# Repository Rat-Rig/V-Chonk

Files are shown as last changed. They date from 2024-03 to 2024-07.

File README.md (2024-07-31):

<a href="https://ratrig.com/">
    RatRig logo RatRig
</a>

# Rat Rig V-Chonk v0.4 BETA
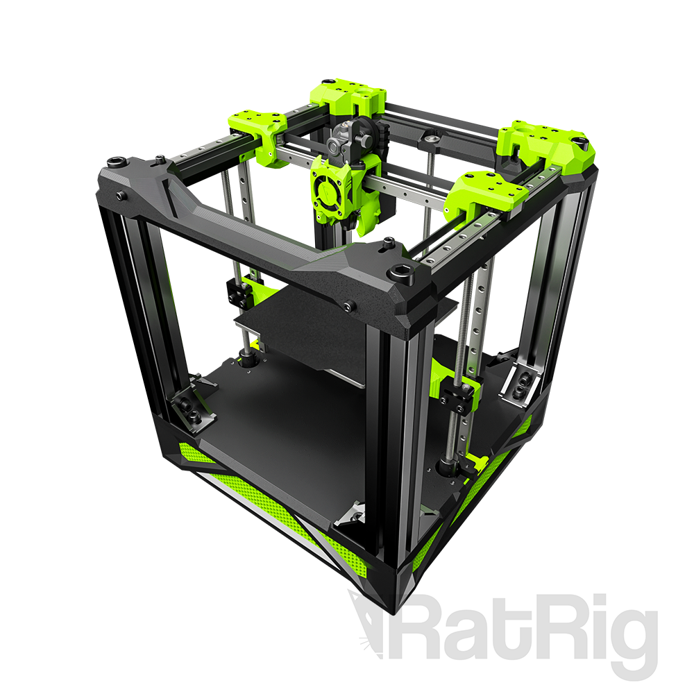
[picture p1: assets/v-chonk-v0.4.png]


## Overview
The Rat Rig V-Chonk is an almost fully 3D printed 3D printer, featuring a CoreXY design and a cubic build volume of 180mm<sup>3</sup>

Full details can be found on [the Rat Rig store](https://ratrig.com/v-chonk-configurable.html), or [the USA Rat Rig store](https://us.ratrig.com/v-chonk-configurable.html)

## Online CAD Viewer
Two different CAD models are available for viewing online:
- [V-Chonk with HF hotend](https://a360.co/3A7DrUY)
- [V-Chonk with UHF hotend](https://a360.co/3A2c6U1)

## STEP Files
Both variants of the CAD model are also available for download in the STEP format:
- [V-Chonk with HF hotend STEP Download](https://files.ratrig.com/cad_models/vchonk/ratrig_v-chonk_v0.4_hf.zip)
- [V-Chonk with UHF hotend STEP Download](https://files.ratrig.com/cad_models/vchonk/ratrig_v-chonk_v0.4_uhf.zip)

## Contributing
This is a fully open source project! We encourage the community at large to mod, upgrade, and share their design variants.

Join our communities and connect with other users, we would love to see some great V-Chonk builds:

Facebook - https://www.facebook.com/groups/ratrig3dprintercommunity

Discord - https://discord.com/invite/ratrig

## License
All files contained within this repository are licensed under the [Creative Commons Attribution-ShareAlike 4.0 International Public License](https://creativecommons.org/licenses/by-sa/4.0/). See LICENSE for the full details.

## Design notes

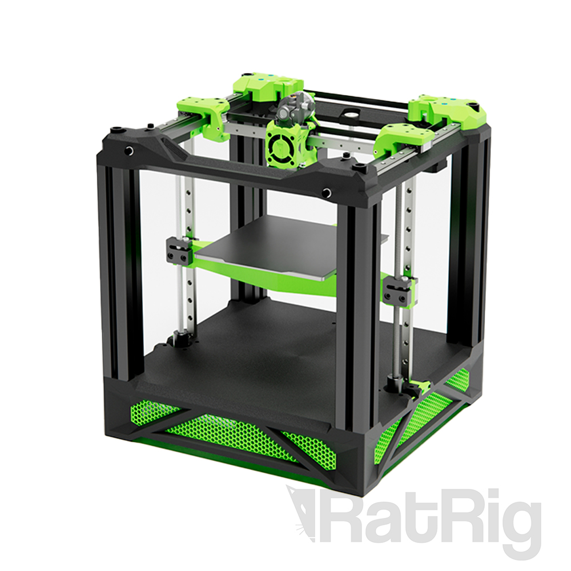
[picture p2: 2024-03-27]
assets/v-chonk-v0.2.jpg

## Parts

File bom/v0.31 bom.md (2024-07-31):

# Bill of Materials

## Printed Parts
| Quantity | Part Name | Link |
| --- | --- | ---- |
| 1x | chonk_base_plate | [chonk_base_plate_V03_20240509.stl](https://github.com/Rat-Rig/V-Chonk/blob/main/stl/Deprecated/chonk_base_plate_V03_20240509.stl) |
| 1x | chonk_bed_carriage | [chonk_bed_carriage_V02_20240606.stl](https://github.com/Rat-Rig/V-Chonk/blob/main/stl/chonk_bed_carriage_V02_20240606.stl) |
| 1x | chonk_belt_pod_a | [chonk_belt_pod_a_V02_20240411.stl](https://github.com/Rat-Rig/V-Chonk/blob/main/stl/chonk_belt_pod_a_V02_20240411.stl) |
| 1x | chonk_belt_pod_b | [chonk_belt_pod_b_V02_20240411.stl](https://github.com/Rat-Rig/V-Chonk/blob/main/stl/Deprecated/chonk_belt_pod_b_V02_20240411.stl) |
| 1x | chonk_belt_pod_c | [chonk_belt_pod_c_V01_20240411.stl](https://github.com/Rat-Rig/V-Chonk/blob/main/stl/Deprecated/chonk_belt_pod_c_V01_20240411.stl) |
| 2x | chonk_belt_tensioner | [chonk_belt_tensioner_x2_V01_20240329.stl](https://github.com/Rat-Rig/V-Chonk/blob/main/stl/chonk_belt_tensioner_x2_V01_20240329.stl) |
| 1x | chonk_motor_cage_a | [chonk_motor_cage_a_V01_20240329.stl](https://github.com/Rat-Rig/V-Chonk/blob/main/stl/chonk_motor_cage_a_V01_20240329.stl) |
| 1x | chonk_motor_cage_b | [chonk_motor_cage_b_V01_20240329.stl](https://github.com/Rat-Rig/V-Chonk/blob/main/stl/chonk_motor_cage_b_V01_20240329.stl) |
| 1x | chonk_skirt_back | [chonk_skirt_back_V01_20240329.stl](https://github.com/Rat-Rig/V-Chonk/blob/main/stl/chonk_skirt_back_V01_20240329.stl) |
| 4x | chonk_skirt_foot | [chonk_skirt_foot_V02_20240509.stl](https://github.com/Rat-Rig/V-Chonk/blob/main/stl/chonk_skirt_foot_V02_20240509.stl) |
| 1x | chonk_skirt_front | [chonk_skirt_front_V01_20240329.stl](https://github.com/Rat-Rig/V-Chonk/blob/main/stl/chonk_skirt_front_V01_20240329.stl) |
| 2x | chonk_skirt_side | [chonk_skirt_side_x2_V01_20240329.stl](https://github.com/Rat-Rig/V-Chonk/blob/main/stl/chonk_skirt_side_x2_V01_20240329.stl) |
| 1x | chonk_toolhead_hf | [chonk_toolhead_hf_V01_20240411.stl](https://github.com/Rat-Rig/V-Chonk/blob/main/stl/Deprecated/chonk_toolhead_hf_V01_20240411.stl) |
| 1x | chonk_toolhead_uhf | [chonk_toolhead_uhf_V01_20240411.stl](https://github.com/Rat-Rig/V-Chonk/blob/main/stl/Deprecated/chonk_toolhead_uhf_V01_20240411.stl) |
| 1x | chonk_xy_gantry | [chonk_xy_gantry_V01_20240329.stl](https://github.com/Rat-Rig/V-Chonk/blob/main/stl/Deprecated/chonk_xy_gantry_V01_20240329.stl) |
| 1x | chonk_xy_joiner_a | [chonk_xy_joiner_a_V01_20240329.stl](https://github.com/Rat-Rig/V-Chonk/blob/main/stl/chonk_xy_joiner_a_V01_20240329.stl) |
| 1x | chonk_xy_joiner_b | [chonk_xy_joiner_b_V01_20240329.stl](https://github.com/Rat-Rig/V-Chonk/blob/main/stl/chonk_xy_joiner_b_V01_20240329.stl) |
| 2x | chonk_z_rail_clamp_bottom | [chonk_z_rail_clamp_bottom_V01_20240329.stl](https://github.com/Rat-Rig/V-Chonk/blob/main/stl/chonk_z_rail_clamp_bottom_V01_20240329.stl) |
| 2x | chonk_z_rail_clamp_top | [chonk_z_rail_clamp_top_x2_V01_20240329.stl](https://github.com/Rat-Rig/V-Chonk/blob/main/stl/chonk_z_rail_clamp_top_x2_V01_20240329.stl) |
| 20x | electronics_wire_guide_clip | [electronics_wire_guide_clip_x20_V01_20240329.stl](https://github.com/Rat-Rig/V-Chonk/blob/main/stl/electronics_wire_guide_clip_x20_V01_20240329.stl) |
| 1x | rr_toolhead_vc3_shroud | [rr_toolhead_vc3_shroud_V01_20240329.stl](https://github.com/Rat-Rig/V-Chonk/blob/main/stl/rr_toolhead_vc3_shroud_V01_20240329.stl) |

### A note regarding the toolhead STLs:
> 
> Depending on your hotend configuration, you will require either **chonk_toolhead_hf** or **chonk_toolhead_uhf**. It is not required to print both.

---
## Hardware
| Quantity | SKU | Part Name |
| --- | --- | --- |
| 3x | HW2205GC | Anti-Backlash Nut Block for 8mm Metric Acme Lead Screw TR8x4 |
| 12x | HW2948WC | Ball Bearing - 695-2RS |
| 24x | HW2947WC | Ball Bearing - F695-2RS |
| 3x | HW1309WC | Ball Bearing F688ZZ Flanged 8 x 16 x 5 |
| 1x | HW2793PC | Bed Plate (V-Minion) - Cast tooling plate - Pre-Machined - 184x184x5mm |
| 8x | HW2038BC | Bracket - Cast 90 Degree Corner for 4040 - 8 Slot - Black |
| 4x | HW3776NC | Brass Heat Insert - M2.5 x 4.0mm (L) x 4.6mm (OD) |
| 65x | HW3224NC | Brass Heat Insert - M3 x 4.0mm (L) x 4.6mm (OD) |
| 3x | HW3791NC | Brass Heat Insert - M4 x 5.8mm (L) x 6.3mm (OD) |
| 8x | HW3131SC | Cap Head Screw M12 (Single) (Length: 45mm) |
| 4x | HW3775SC | Cap Head Screw M2.5 (Single) (Length: 6mm) |
| 8x | HW1292SC | Cap Head Screw M3 (Single) (Length: 12mm) |
| 6x | HW1507SC | Cap Head Screw M3 (Single) (Length: 16mm) |
| 20x | HW1504SC | Cap Head Screw M3 (Single) (Length: 20mm) |
| 8x | HW1228SK | Cap Head Screw M3 (Single) (Length: 45mm) |
| 35x | HW1502SC | Cap Head Screw M3 (Single) (Length: 8mm) |
| 3x | HW1192SC | Cap Head Screw M4 (Single) (Length: 8mm) |
| 25x | HW1285SC | Cap Head Screw M5 (Single) (Length: 10mm) |
| 6x | HW1055SC | Cap Head Screw M5 (Single) (Length: 25mm) |
| 2x | HW1058SC | Cap Head Screw M5 (Single) (Length: 30mm) |
| 8x | HW2074SC | Cap Head Screw M5 (Single) (Length: 45mm) |
| 2x | HW2139SC | Cap Head Screw M5 (Single) (Length: 50mm) |
| 4x | HW2957SC | Cap Head Screw M5 (Single) (Length: 65mm) |
| 8x | HW2164SC	| Cap Head Screw M8 (Single) (Length: 16mm) |
| 8x | HW3130SC | Cap Head Screw M8 (Single) (Length: 25mm) |
| 3x | HW3934SC | Countersink Screw M4 (Single) (Length: 50mm) |
| 3x | HW2990GC | Coupler - Rigid Type - Black 25x20mm - 5mm to 8mm |
| 8x | HW2171NC	| T-Nut - Drop In Type for 40 Series - M8 (Single) |
| 22x | HW1039NC | Hex Locking Nut - M5 |
| 8x | HW3211NC | Hex Locking Nut - M8 |
| 3x | - | Leadscrew - TR8x4 - 290mm |
| 3x | HW2352GC | Linear Rail - MGN12 250mm + MGN12C carriage |
| 2x | HW2911GC | Linear Rail - MGN12 300mm + MGN12C carriage |
| 4x | HW2125GC | Rubber foot with metal insert - Heavy Duty - 28x22x16.5mm |
| 1x | HW3499SC | Set Screw M3 x 5mm |
| 21x | HW1630NC | Shim - Mini Precision Shim - 8 x 5 x 1mm |
| 3x | HW2792NC | Spacer - Stainless Steel - 12mm (Length) x 4.1mm (ID) x 8mm (OD) |
| 4x | HW441BRC | T-SLOT 4040 - Black Anodized 280mm |
| 2.5x | HW1653GC | Timing Belt  - 2GT 9mm (By the meter) |
| 2x | HW1654WC | Timing Pulley - 2GT (2mm) - 20 Tooth - For 9mm Belt - 5mm Bore |
| 2x | HW1818NC | Washer Simple M3 - Nylon - 7mm x 3.2mm x 0.5mm |
| 3x | HW2848NC | Washer Simple M4 - Nylon - 8mm x 4mm x 1mm |
| 6x | HW1315NC | Washer Simple M5 |
| 16x | HW3124NC | Washer Simple M8 |

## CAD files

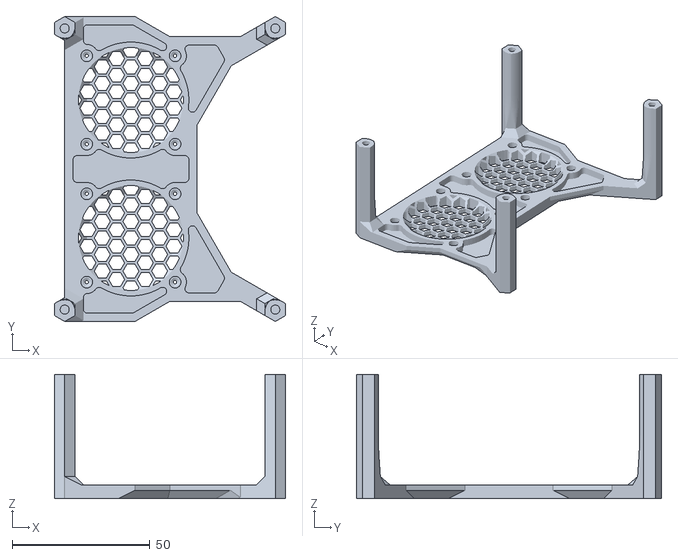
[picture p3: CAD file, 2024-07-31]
stl/chonk_mainboard_cooler_V01_20240730.stl
83.8 x 110.5 x 45.0

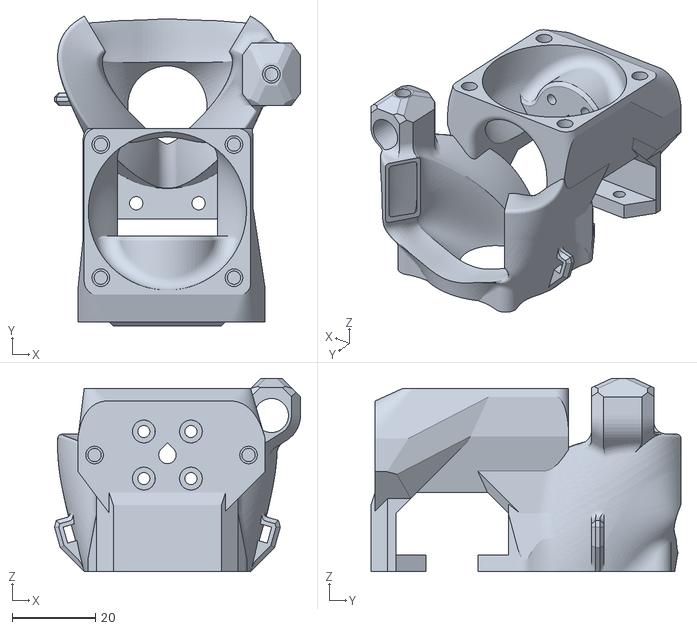
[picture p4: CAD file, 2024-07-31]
stl/chonk_toolhead_hf_V02_20240730.stl
59.1 x 74.5 x 46.4

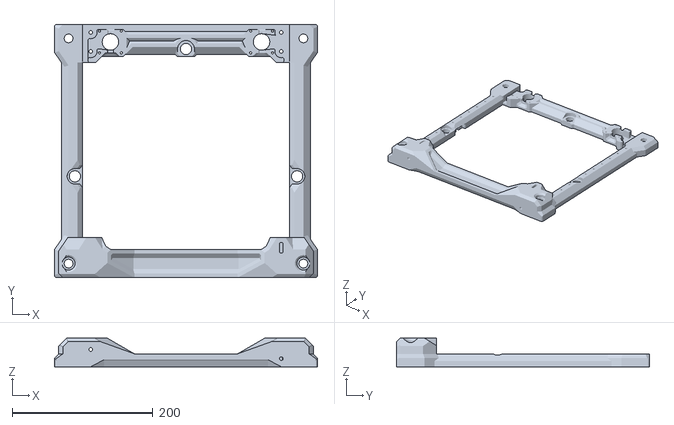
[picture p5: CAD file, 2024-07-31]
stl/chonk_xy_gantry_V02_20240730.stl
373.8 x 360.0 x 40.8

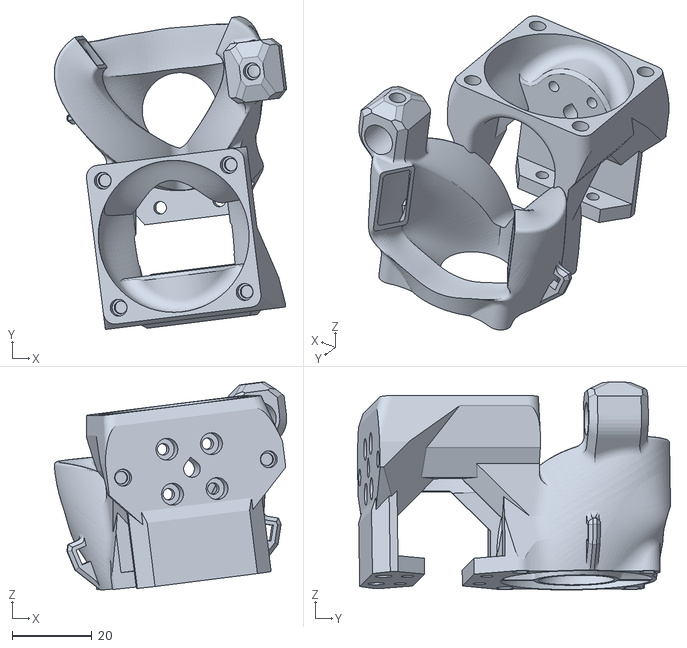
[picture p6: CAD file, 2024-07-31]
stl/chonk_toolhead_uhf_V02_20240730.stl
58.1 x 78.3 x 52.0

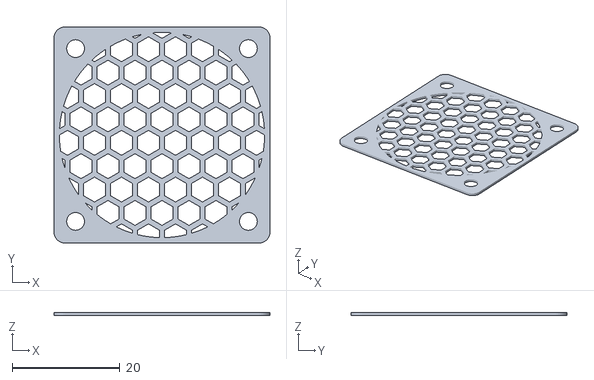
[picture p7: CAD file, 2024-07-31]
stl/40mm_fan_cage_V01_20240730.stl
40.0 x 40.0 x 0.6

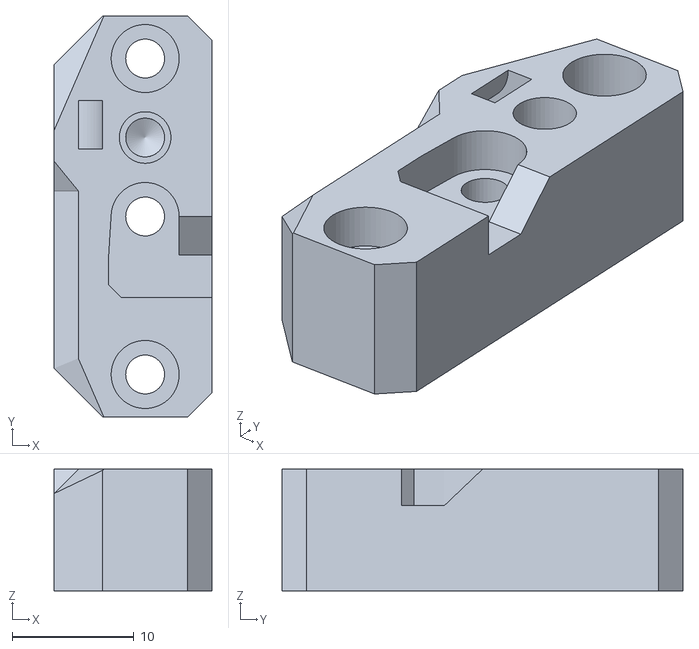
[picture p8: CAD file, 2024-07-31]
stl/chonk_belt_pod_b_V03_20240730.stl
13.0 x 33.0 x 10.0

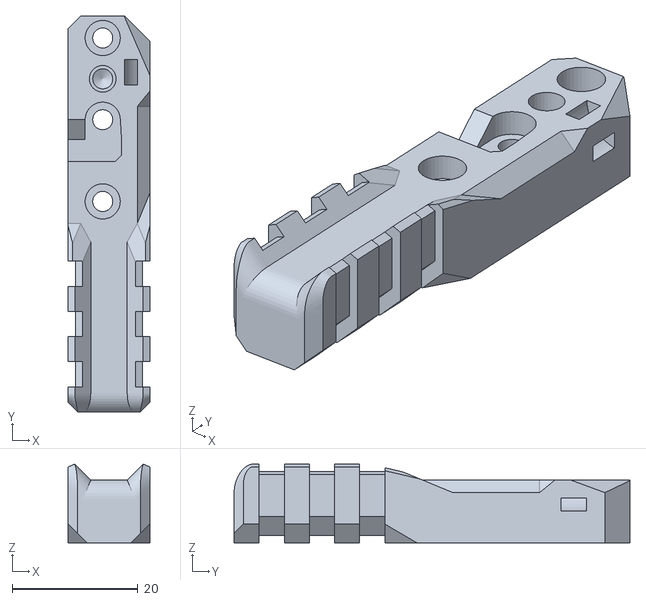
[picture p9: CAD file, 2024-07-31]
stl/chonk_belt_pod_c_V02_20240730.stl
13.0 x 63.0 x 12.5

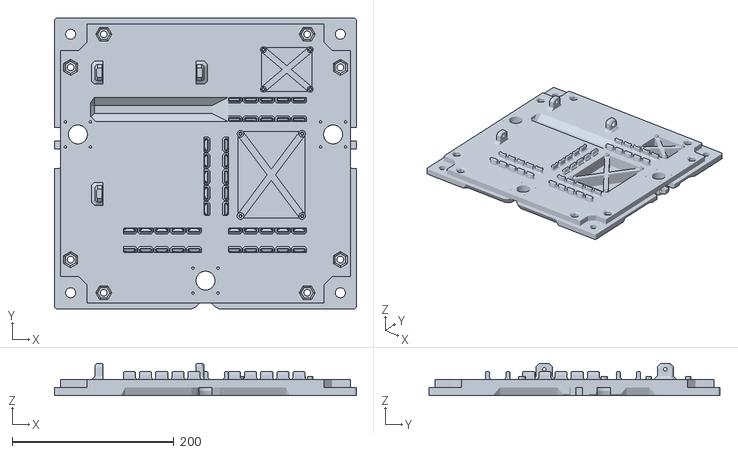
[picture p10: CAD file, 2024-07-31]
stl/chonk_base_plate_V04_20240730.stl
373.8 x 360.0 x 40.0

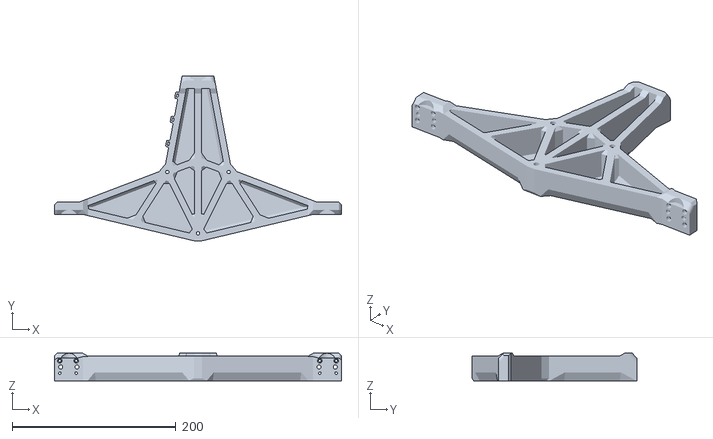
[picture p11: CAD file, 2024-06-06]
stl/chonk_bed_carriage_V02_20240606.stl
351.0 x 201.3 x 33.7

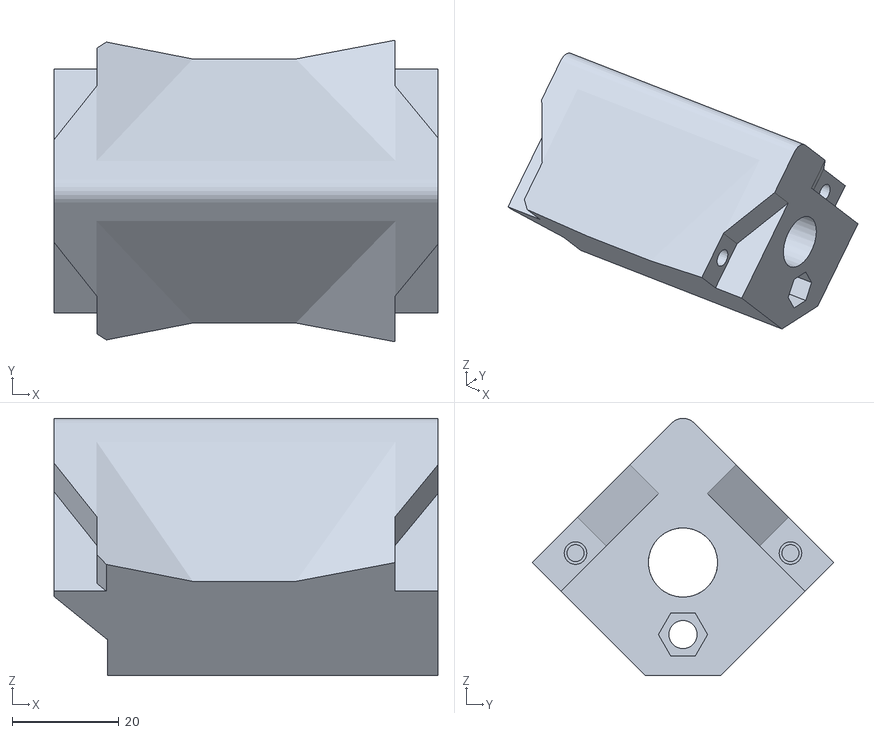
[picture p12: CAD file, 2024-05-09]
stl/chonk_skirt_foot_V02_20240509.stl
72.0 x 56.5 x 48.3

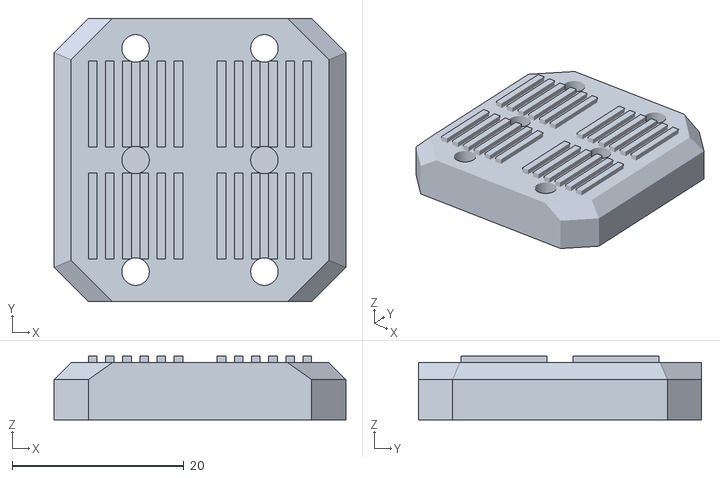
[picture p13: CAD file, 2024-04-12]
stl/chonk_belt_pod_a_V02_20240411.stl
34.0 x 33.0 x 7.45

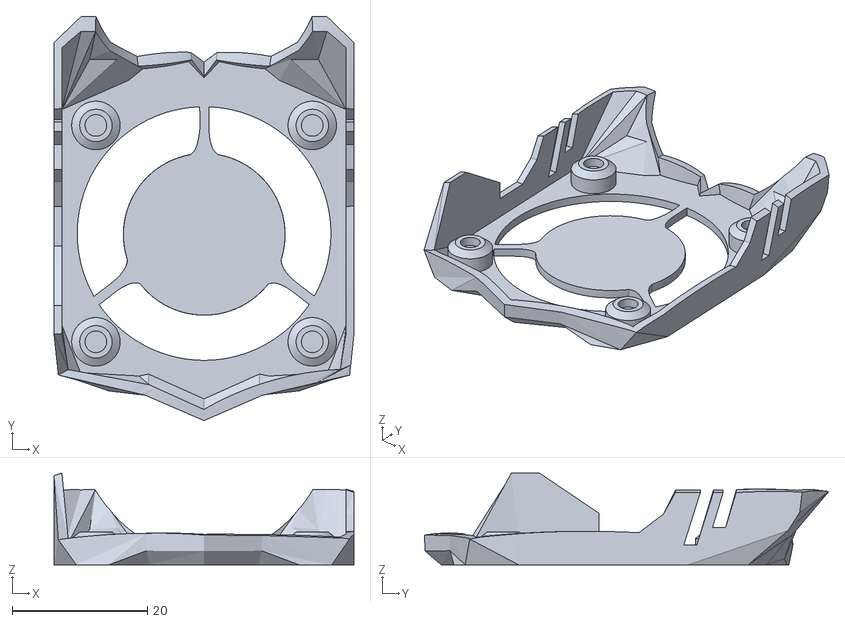
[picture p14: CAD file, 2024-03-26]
stl/rr_toolhead_vc3_shroud_V01_20240329.stl
44.4 x 59.8 x 13.6

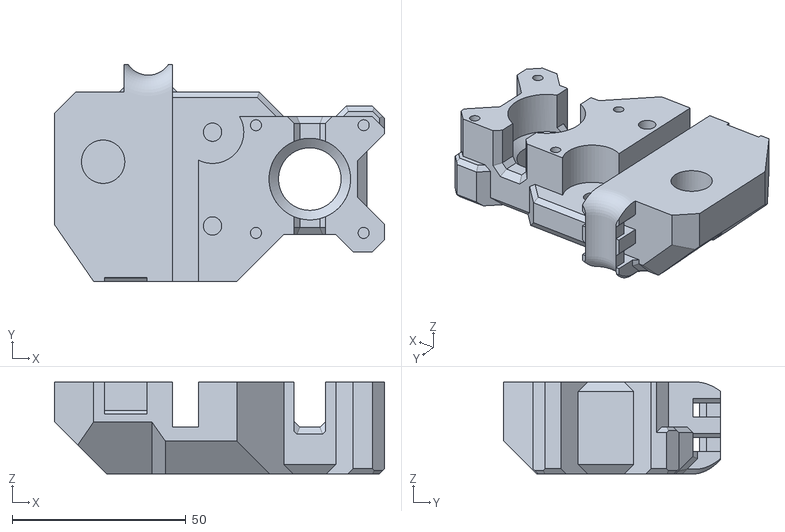
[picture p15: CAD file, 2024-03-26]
stl/chonk_motor_cage_b_V01_20240329.stl
95.0 x 62.5 x 26.5

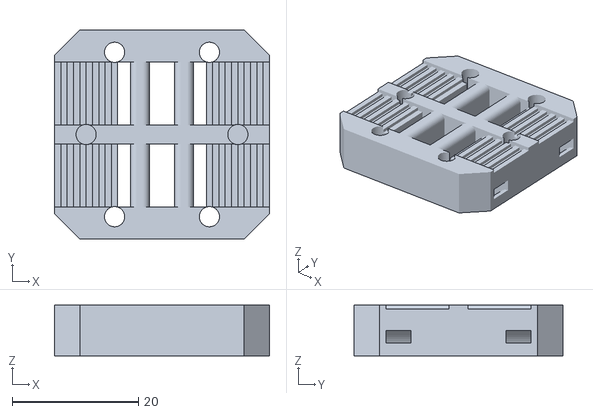
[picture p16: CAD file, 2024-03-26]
stl/chonk_belt_pod_b_V01_20240329.stl
34.0 x 33.0 x 8.00

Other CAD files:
stl/chonk_base_plate_V02_20240426.stl
stl/chonk_base_plate_V01_20240329.stl
stl/electronics_wire_guide_clip_x20_V01_20240329.stl
stl/chonk_xy_joiner_b_V01_20240329.stl
stl/Deprecated/chonk_base_plate_V01_20240329.stl
stl/Deprecated/chonk_base_plate_V02_20240426.stl
stl/Deprecated/chonk_base_plate_V03_20240509.stl
stl/Deprecated/chonk_bed_carriage_V01_20240329.stl
stl/Deprecated/chonk_belt_pod_a_V01_20240329.stl
stl/Deprecated/chonk_belt_pod_b_V02_20240411.stl
stl/Deprecated/chonk_belt_pod_c_V01_20240411.stl
stl/Deprecated/chonk_skirt_foot_V01_20240329.stl
stl/Deprecated/chonk_toolhead_hf_V01_20240411.stl
stl/Deprecated/chonk_toolhead_uhf_V01_20240411.stl
stl/Deprecated/chonk_xy_gantry_V01_20240329.stl
stl/chonk_bed_carriage_V01_20240329.stl
stl/chonk_belt_pod_a_V01_20240329.stl
stl/chonk_belt_tensioner_x2_V01_20240329.stl
stl/chonk_motor_cage_a_V01_20240329.stl
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

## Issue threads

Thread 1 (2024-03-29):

Missing Part on BOM

lost-hope, 2024-03-29:
While reviewing the STEP and the BOM i saw that the SKRAT is missing.

Closed 2024-04-01.

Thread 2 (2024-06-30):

Electronics and toolhead BOM missing

kozross, 2024-06-30:
Looking at the CAD models, I can infer that the control board is meant to be a BTT SKRat, and the 'HF' option looks like a Dragon Ace, while the 'UHF' option looks like a Rapido, but it would be good to get a clear list of what electronics and toolhead components are required for the build.

Also, are those two going to be the only officially-supported hotends?

Edit: it seems the electronics section was removed in [this commit](https://github.com/Rat-Rig/V-Chonk/commit/52b672ddd3f10c12f0c60cb8d6374e726834bc68) and never got replaced.

Closed 2024-07-31.

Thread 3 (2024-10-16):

Req: Filament requirements and print specs

hreality, 2024-10-16:
Doing a 'test' to see if this will hold on my 400 build plate and its looking pretty good.  Could the BOM be updated or the code to reflect print specs and filament requirements?

akryll, 2025-01-27:
please

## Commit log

2024-03-26 Add v0.2 CAD Assembly
2024-03-26 Add v0.2 STL files
    [chonk_base_plate_V01_20240329.stl, chonk_bed_carriage_V01_20240329.stl, chonk_belt_pod_a_V01_20240329.stl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]
2024-03-26 Add v0.2 Bill of Materials
2024-03-26 Add missing shroud STL
    [rr_toolhead_vc3_shroud_V01_20240329.stl]
2024-03-29 Update v0.2 CAD, BOM & Base Plate STL
    [chonk_base_plate_V01_20240329.stl]
2024-03-29 Add link to Fusion CAD viewer
2024-03-29 Update v0.2 bom.md
    Correct formatting issues caused by Markdown
2024-04-01 Remove electronics section from BOM
    To be corrected, this also closes #1
2024-04-11 Update BOM with STL links
2024-04-12 V-Chonk v0.3 Release
    [chonk_belt_pod_a_V01_20240329.stl, chonk_belt_pod_a_V02_20240411.stl, chonk_belt_pod_b_V01_20240329.stl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]
2024-04-26 Add UHF CAD variant
2024-04-26 Update chonk_base_plate
    An issue was identified where the M8 hex nut cut-outs were incorrectly sized.
    [chonk_base_plate_V01_20240329.stl, chonk_base_plate_V02_20240426.stl]
2024-05-09 V-Chonk v0.31 Release
    [chonk_base_plate_V02_20240426.stl, chonk_base_plate_V03_20240509.stl, chonk_skirt_foot_V01_20240329.stl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]
2024-06-06 BOMs: Correct chonk_bed_gantry naming
    Entries for chonk_bed_gantry in the BOMs should be named chonk_bed_carriage to match the STL filename
2024-06-06 Update chonk_bed_carriage for v0.3 & v0.31
    This updated part was missed in the v0.3 release, and thus was missing in v0.31 as well
    [chonk_bed_carriage_V01_20240329.stl, chonk_bed_carriage_V02_20240606.stl]
2024-07-31 V-Chonk v0.4 Release
    [40mm_fan_cage_V01_20240730.stl, chonk_base_plate_V03_20240509.stl, chonk_base_plate_V04_20240730.stl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]
2024-07-31 Add electronics details to v0.4 BOM
    Closes #2
